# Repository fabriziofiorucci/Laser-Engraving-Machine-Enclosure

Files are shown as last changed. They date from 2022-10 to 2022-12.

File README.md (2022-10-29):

# Laser Engraving Machine Enclosure

This is an enclosure project to safely run a 450mm x 450mm laser engraving open frame machine.
The project was originally built around Sculpfun S9 but is suitable for all laser engraving machines with a footprint up to 450mm x 450mm.

Features:

- Full enclosure to protect from laser beam
- Air assist support
- Camera support to keep track of ongoing engraving/cutting jobs
- Internal lighting
- Fumes exhaust system
- Controlled by Wemos Lolin D1 mini
  - Pushbuttons and OLED display
  - Fumes exhaust system start/stop
  - Air assist start/stop
  - Laser engraver start/stop
- MQTT support (work in progress)

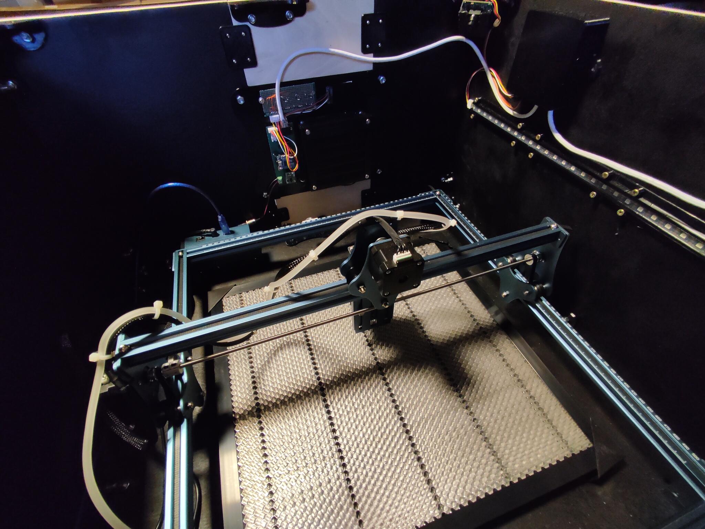
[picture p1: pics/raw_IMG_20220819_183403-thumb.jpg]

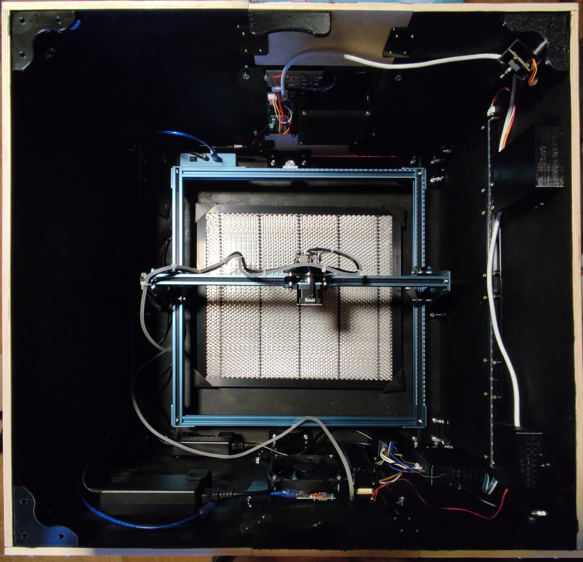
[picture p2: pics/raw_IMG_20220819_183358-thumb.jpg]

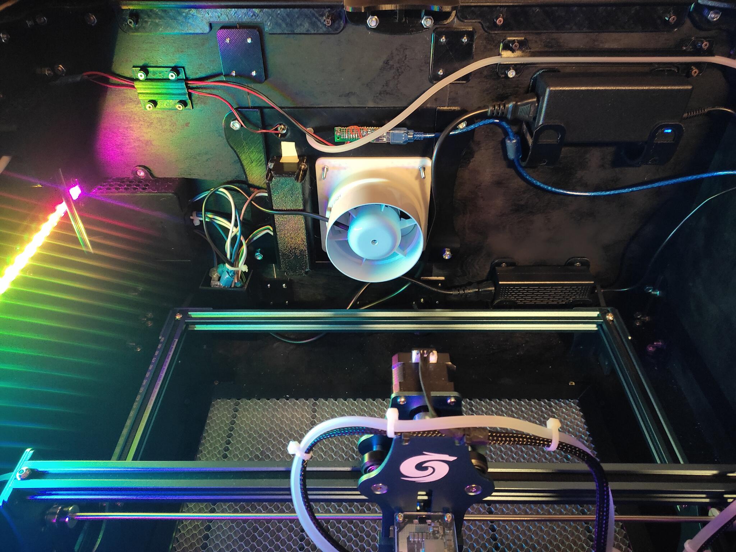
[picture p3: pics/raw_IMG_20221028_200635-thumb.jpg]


## Main structure

The main structure is built with 10mm-thick medium-density fiberboard (MDF) panels, spray-painted black.

## 3D Printed parts

The complete Fusion 360 project can be found in the [CAD folder](/CAD) and it can be opened in Autodesk Fusion 360.

3D parts should be printed using:

- Black PLA or PETG
- 20% infill
- 0.1mm layer width
- 4 walls
- No supports required for most parts

## Microcontroller

The [sketch](/sketch) can be flashed to Wemos Lolin D1 mini using Arduino 1.8.7 or later

NOTE: don't forget to use the provided User_Setup.h instead of the stock file that comes with the TFT_eSPI library

Required external libraries are:

- PCF8574 library by Renzo Mischianti - https://www.mischianti.org/2019/01/02/pcf8574_1-i2c-digital-i-o-expander-fast-easy-usage/
- APA102 by Pololu
- TFT_eSPI by Bodmer
- PubSubClient by Nick O'Leary
- NTPClient by Fabrice Weinberg

Display bitmaps have been generated using [LCD Image Converter](https://sourceforge.net/projects/lcd-image-converter/)

## Bill of Materials

### Main structure:

- 2x MDF boards 700mm x 700mm x 10mm
- 2x MDF boards 700mm x 400mm x 10mm
- 2x MDF boards 400mm x 300mm x 10mm
- 2x MDF boards 400mm x 200mm x 10mm
- 4x MDF boards 200mm x 100mm x 10mm
- Black spray paint ([RAL 9005](https://www.ralcolorchart.com/ral-classic/ral-9005-jet-black), approx 800ml needed)

### 3D-printed parts:

- 2kg black PLA or PETG filament

### Air Assist:

- 1x Hailea Air Compressor ACO-318 or equivalent (60L/min, 230V)
- Flexible air-line aquarium tubing, 4mm inner diameter, 6mm outer diameter

### Fumes exhaust system:

- 2x 120mm 12v PC fan
- 1x Airope BA 100mm Axial inline 100mm diameter fumes extractor fan or equivalent
- 1x Flexible Fume Hood Duct 102mm diameter

### Electronics:

Full schematics are [available here](/schematics). All boards built on single-sided protoboard.

#### Main board

- 1x Wemos Lolin D1 mini
- 1x MP1584EN (DC-DC 3A step-down)
- 1x PCF8574 (I2C I/O expansion module)
- 1x P82B715PN (I2C bus extender)
- 1x 2-pin PCB terminal block
- 1x RJ45 8p8c 90 degree angle PCB connector
- 1x 5-pin JST XH2.54 PCB terminal connector
- 1x 4-pin JST XH2.54 PCB terminal connector
- 1x 2-pin JST XH2.54 PCB terminal connector
- 1x 2n2222a transistor
- 3x 1kOhm 1/4w resistor
- 2x 430Ohm 1/4w resistor
- 2x 4.7kOhm 1/4w resistor
- 1x 1n4148 diode
- 1x 8pin DIP socket
- 1x 16pin DIP socket

#### Control and display board

- 1x IPS LCD 1.3" 240×240 RGB Display ST7789 (ie. https://protosupplies.com/product/ips-lcd-1-3-240x240-rgb-display-st7789/)
- 3x 4-pin tactile pushbutton momentary switch with switch cap (ie. https://www.amazon.com/TWTADE-Momentary-Tactile-Button-12x12x12mm/dp/B07CG7VTGD)
- 1x 5-pin JST XH2.54 PCB terminal connector
- 3x 0.1uF capacitor
- 3x 100kOhm 1/4w resistor
- 3x 10kOhm 1/4w resistor

#### Port expander board

- 1x MP1584EN (DC-DC 3A step-down)
- 1x PCF8574 (I2C I/O expansion module)
- 1x P82B715PN (I2C bus extender)
- 2x RJ45 8p8c 90 degree angle PCB connector
- 1x 3-pin JST XH2.54 PCB terminal connector
- 1x 4-pin JST XH2.54 PCB terminal connector
- 2x 2n2222a transistor
- 6x 1kOhm 1/4w resistor
- 2x 430Ohm 1/4w resistor
- 2x 4.7kOhm 1/4w resistor
- 1x 1n4148 diode
- 1x 8pin DIP socket
- 1x 16pin DIP socket

#### Port splitter board

- 1x RJ45 8p8c 90 degree angle PCB connector
- 1x 2-pin JST XH2.54 PCB terminal connector

#### Relay board

- 1x 5v Relay board 4 channels

#### Other / miscellaneous

- 1x APA102 RGB LED weatherproof strip (38 LEDs needed)
- 1x 1/3" 480TVL CCD, 12v color camera board with analog output or equivalent (ie. https://www.aliexpress.com/item/1005004590992499.html)
- 1x RCA female panel mount connector
- 1x micro USB to DIP adapter (ie. https://www.aliexpress.com/item/32970950859.html)
- 1x USB Type A female PCB connector
- 0.1" Strip male headers
- CAT6 cable
- RJ45 8p8c plugs for CAT6 cable

### Hardware:

- M3, M4 and M6 torx screws
- M3, M4 and M6 nuts
- Zip ties

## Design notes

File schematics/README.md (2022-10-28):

# Electronic schematics

All schematics created with [EasyEDA](https://easyeda.com).
Boards can be built using single-sided protoboard

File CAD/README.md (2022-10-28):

# Autodesk Fusion 360 project files

These files can be opened in Fusion 360 to generate stl output for 3D printing.

3D parts should be printed using:

- Black PLA or PETG
- 20% infill
- 4 walls
- No supports required for most parts

[STL files](/CAD/stl) are provided as well.

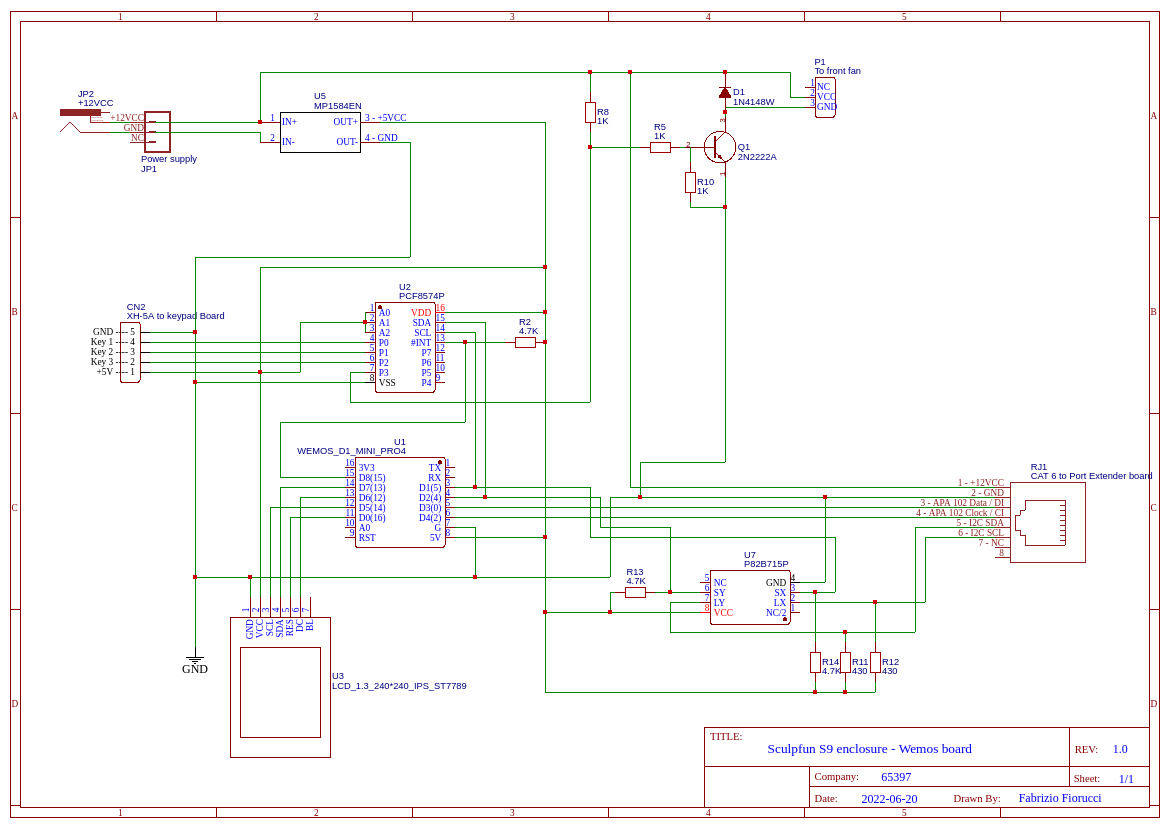
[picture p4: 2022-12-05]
schematics/Wemos board.png

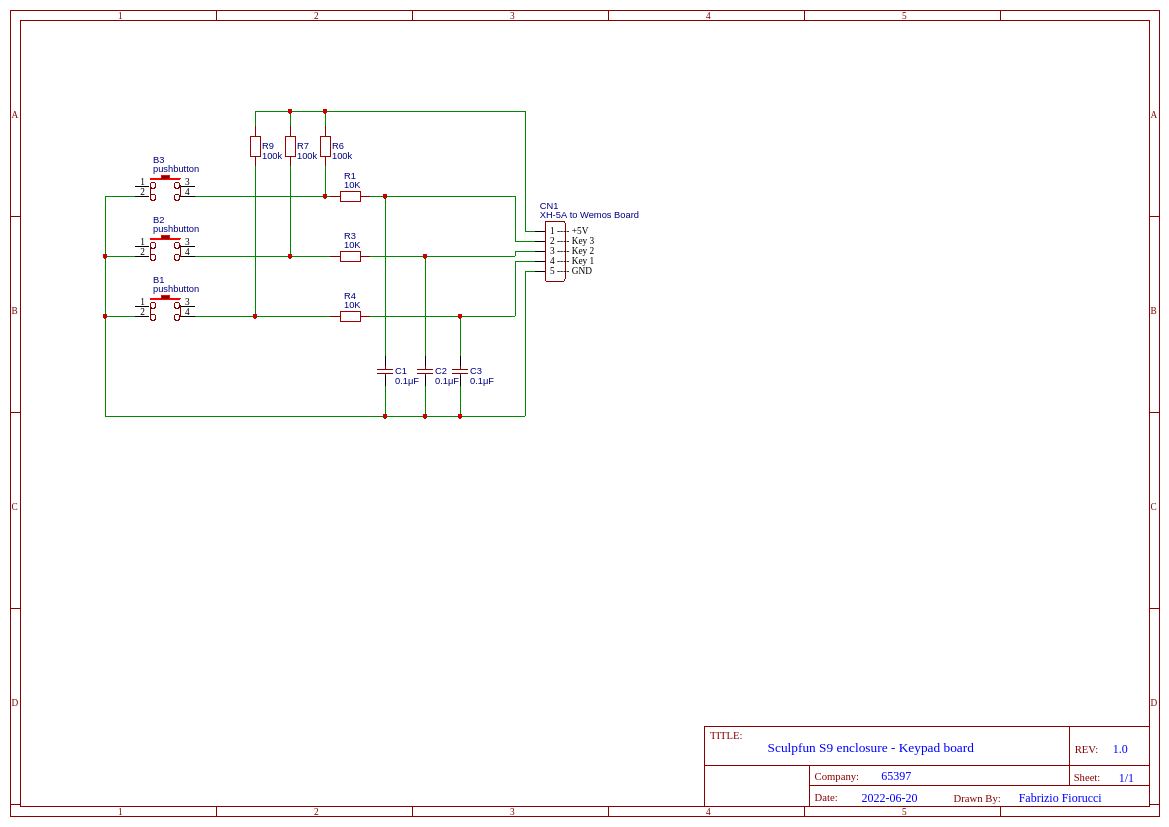
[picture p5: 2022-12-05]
schematics/Keypad board.png

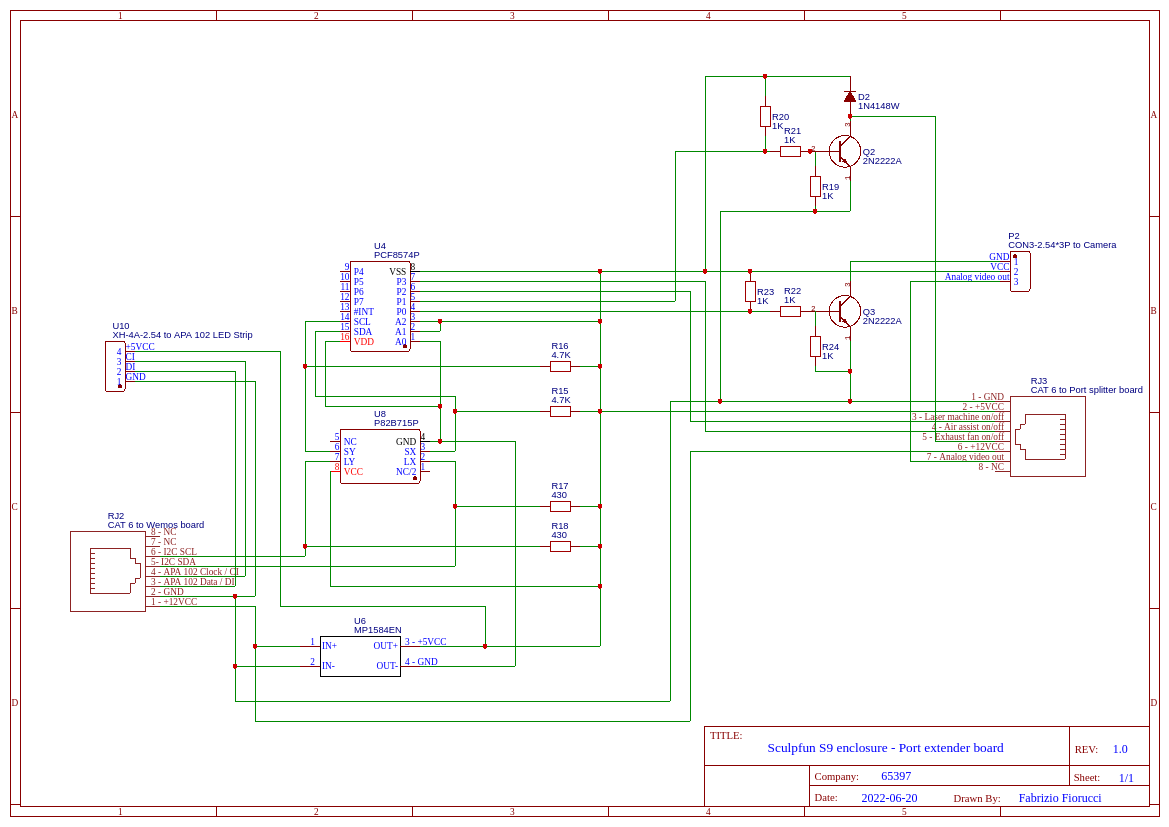
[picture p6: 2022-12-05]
schematics/Port extender board.png

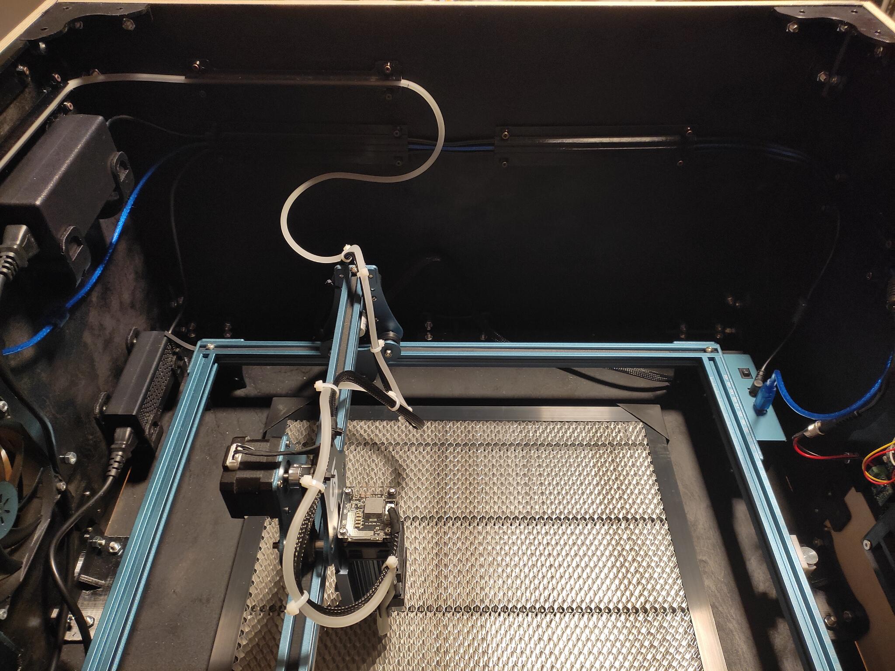
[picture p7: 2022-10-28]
pics/raw_IMG_20220917_213138-thumb.jpg

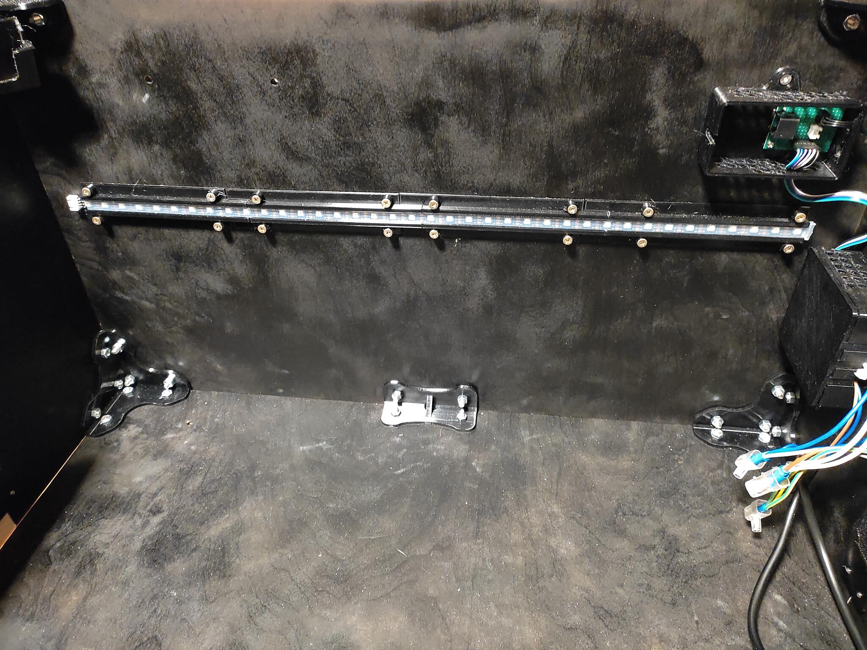
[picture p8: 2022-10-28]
pics/raw_IMG_20220808_000309-thumb.jpg

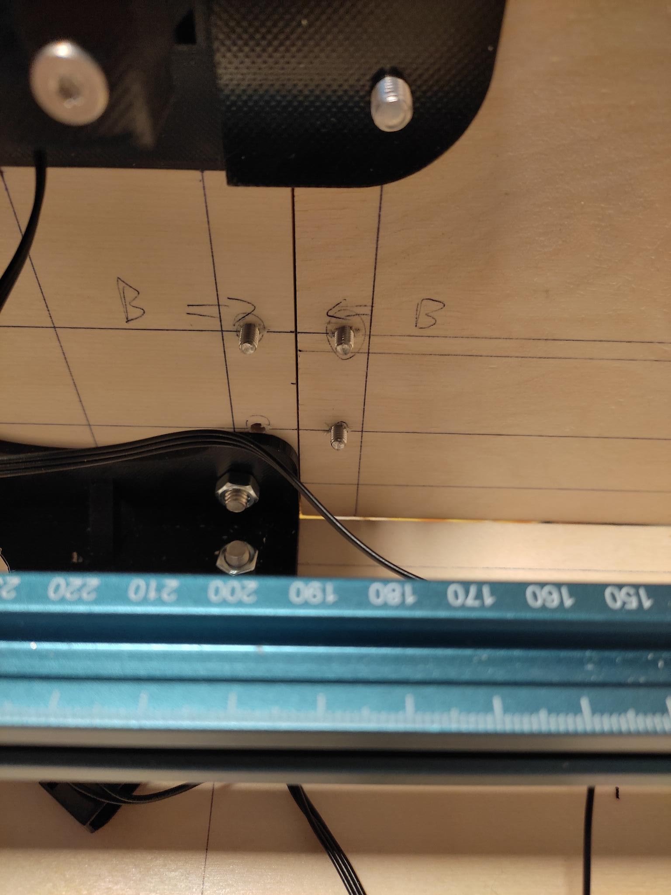
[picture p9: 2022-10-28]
pics/raw_IMG_20220528_145532-thumb.jpg

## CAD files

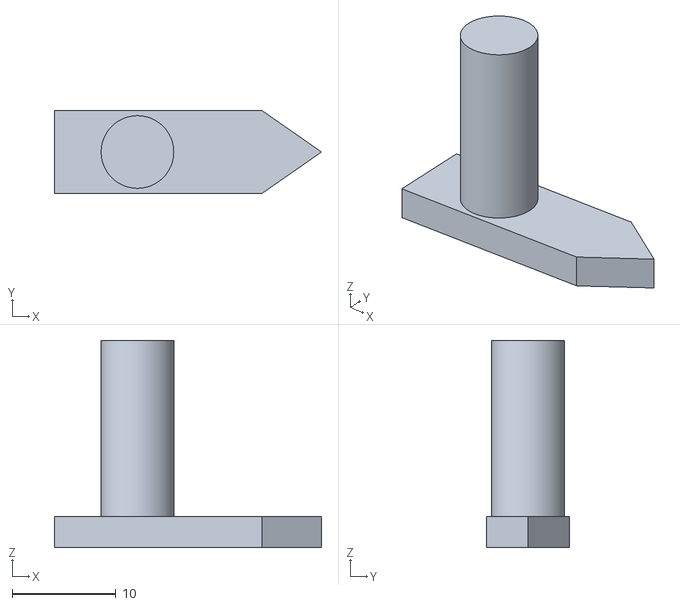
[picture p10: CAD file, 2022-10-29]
CAD/stl/Honeycomb bed pin.stl
25.7 x 8.00 x 20.0

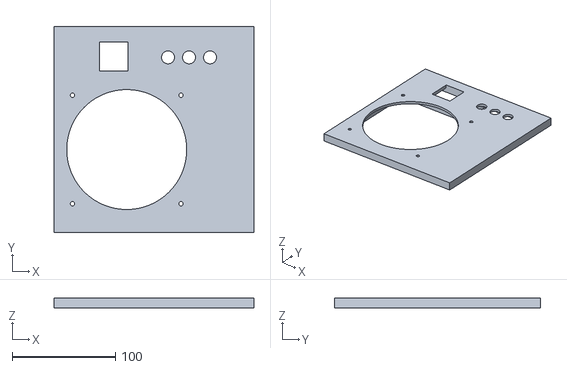
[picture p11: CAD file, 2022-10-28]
CAD/stl/Front panel.stl
193.5 x 199.5 x 10.0

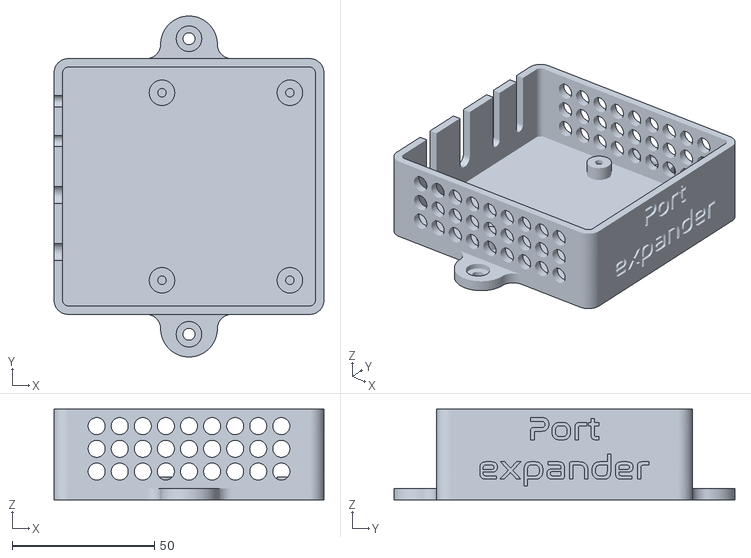
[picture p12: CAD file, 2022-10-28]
CAD/stl/Port expander base.stl
95.0 x 120.0 x 32.0

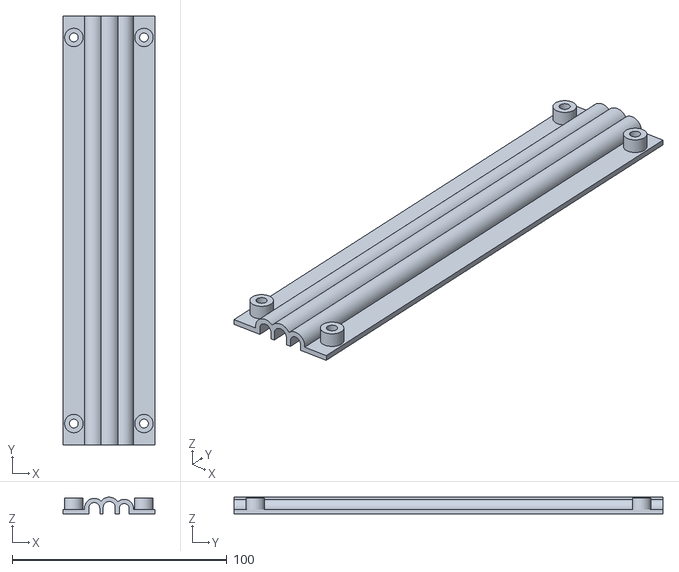
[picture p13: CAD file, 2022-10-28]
CAD/stl/Power and USB cable guide.stl
42.8 x 200.0 x 7.80

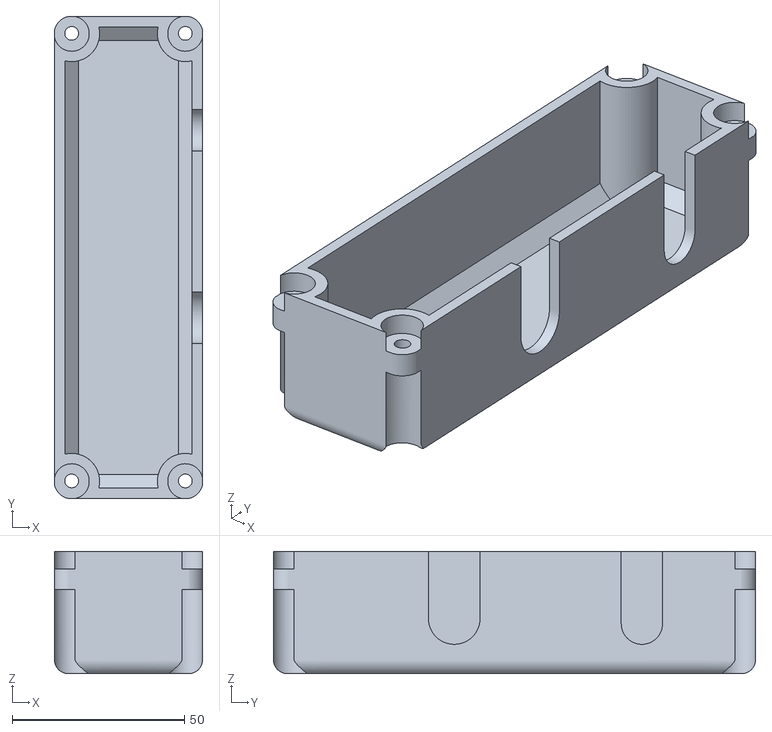
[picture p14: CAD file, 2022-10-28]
CAD/stl/Back panel 220v lid.stl
43.0 x 140.0 x 35.5

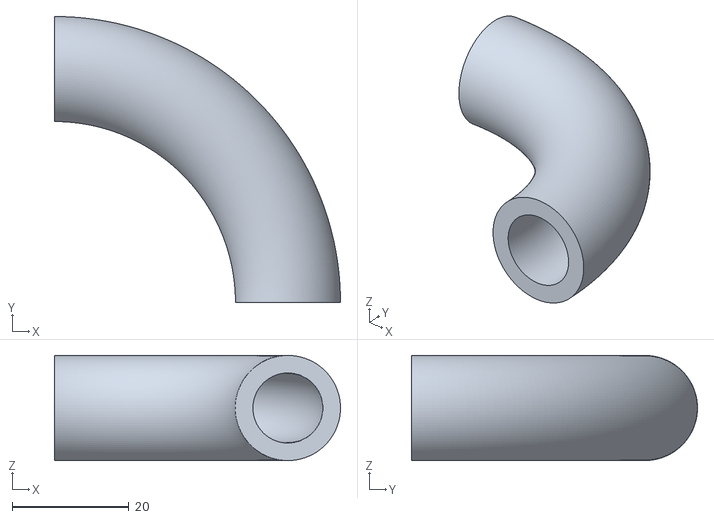
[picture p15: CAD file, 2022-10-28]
CAD/stl/Air compressor guide.stl
49.0 x 49.0 x 18.0

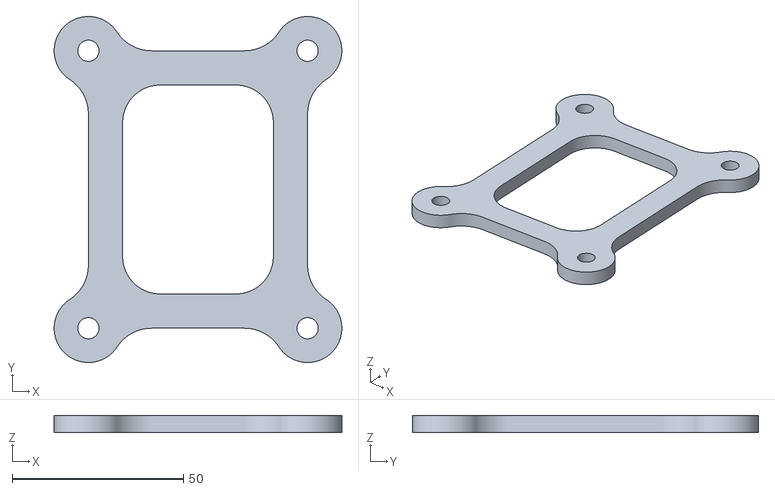
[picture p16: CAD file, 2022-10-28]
CAD/stl/Air compressor bracket.stl
84.0 x 101.0 x 5.00

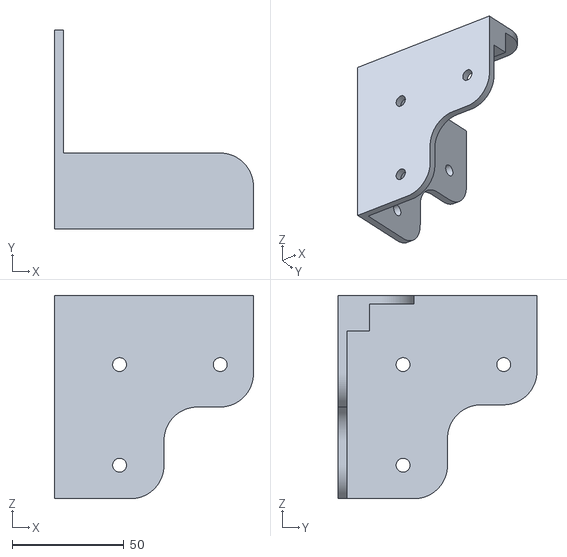
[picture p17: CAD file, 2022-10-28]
CAD/stl/Top cover corner lock 1.stl
89.0 x 89.0 x 91.0

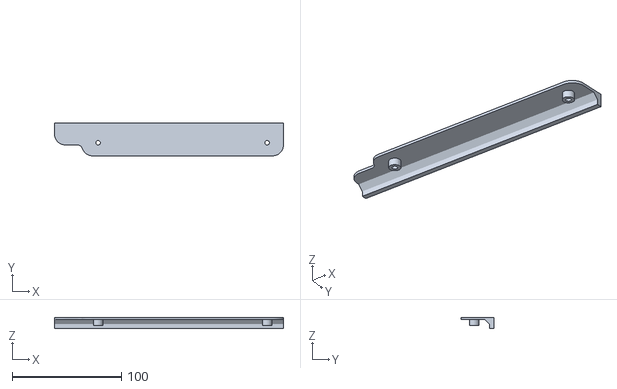
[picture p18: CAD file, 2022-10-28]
CAD/stl/Darkening corner 2.stl
210.0 x 30.0 x 10.0

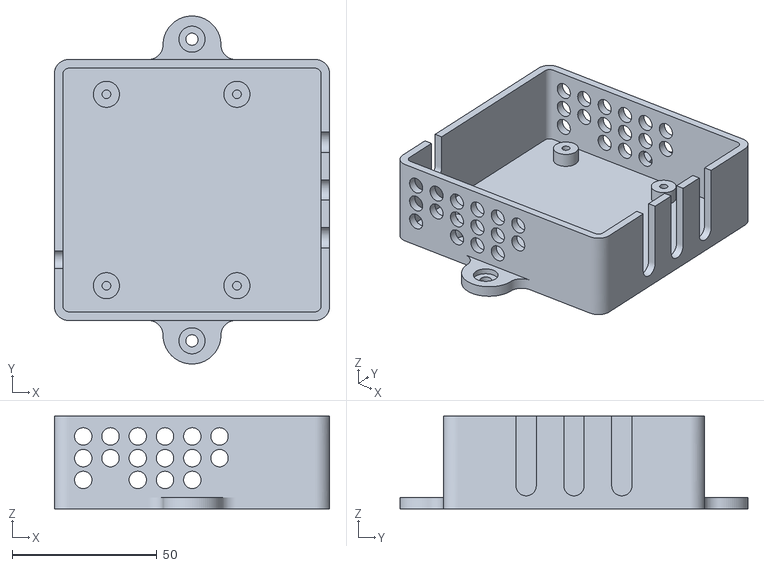
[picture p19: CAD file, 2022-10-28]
CAD/stl/Relay box base.stl
95.0 x 120.0 x 32.0

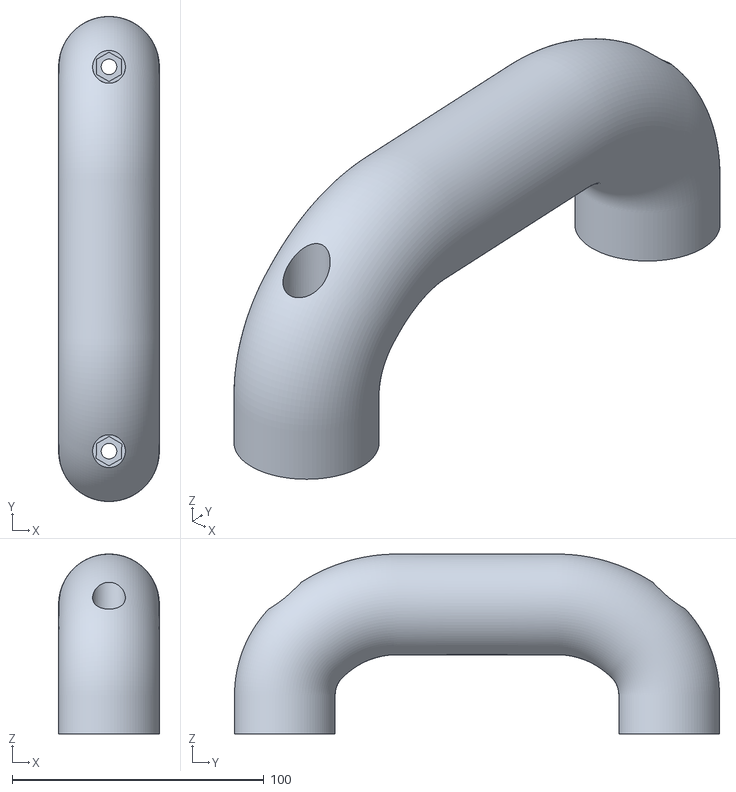
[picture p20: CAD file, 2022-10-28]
CAD/stl/Top handle v8.stl
40.0 x 192.5 x 71.4

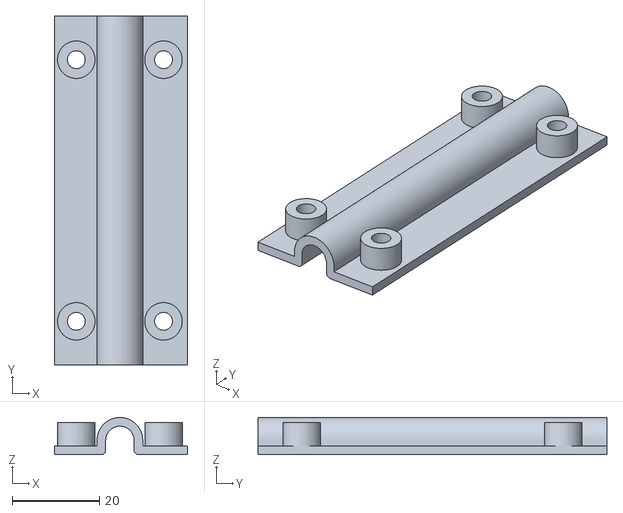
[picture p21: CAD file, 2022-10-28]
CAD/stl/Cat 6 cable guide.stl
30.5 x 80.0 x 8.50

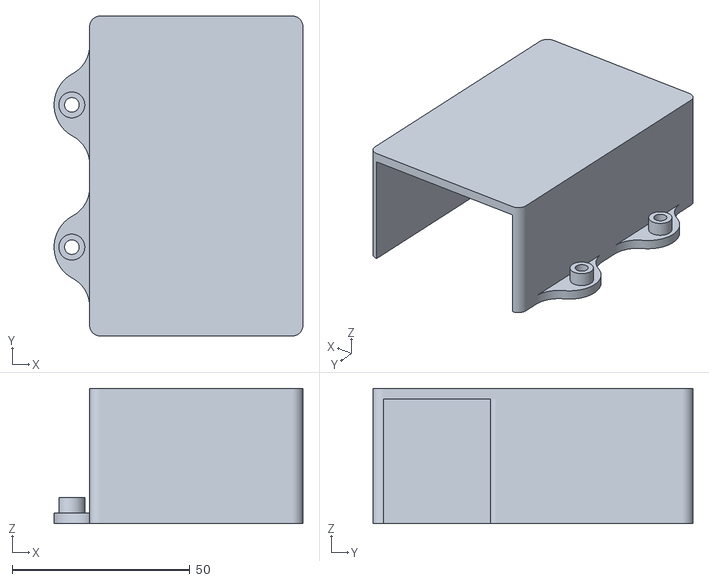
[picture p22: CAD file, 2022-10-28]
CAD/stl/230V protection shell v12.stl
70.0 x 90.0 x 38.0

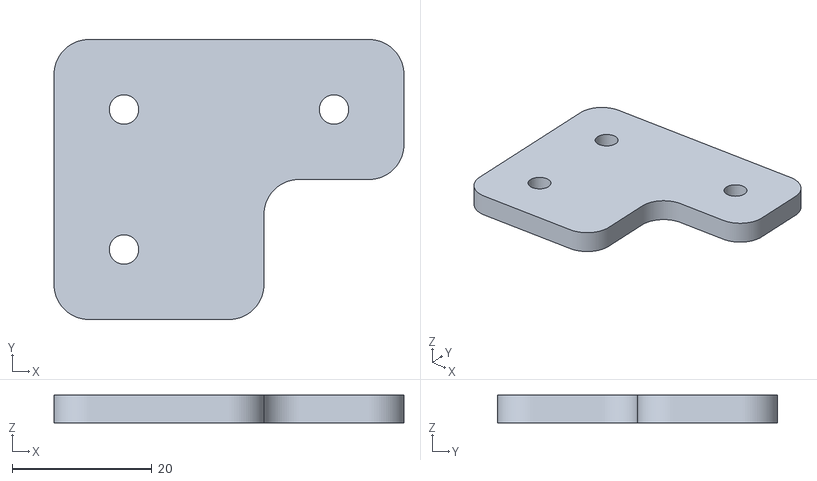
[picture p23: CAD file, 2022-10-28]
CAD/stl/Panel holder mini 3 holes v2.stl
50.0 x 40.0 x 4.00

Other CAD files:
CAD/stl/Camera output and fan cables.stl
CAD/stl/USB port lid.stl
CAD/stl/Exhaust pipe bracket v7.stl
CAD/stl/PSU 8A holder v17Left.stl
CAD/Exhaust pipe external bracket v9.f3d
CAD/Honeycomb bed pin v2.f3d
CAD/Laser air tube clip v11.f3d
CAD/stl/APA102 Led guide end v4.stl
CAD/stl/APA102 Led guide mid v7.stl
CAD/stl/APA102 Led guide start v12.stl
CAD/stl/Air pipe guide 200mm.stl
CAD/stl/Back Panel.stl
CAD/stl/Camera bracket v25.stl
CAD/stl/Corner bracket v22.stl
CAD/stl/Darkening corner 1.stl
CAD/stl/Darkening corner style 2.1.stl
CAD/stl/Darkening corner style 2.2.stl
CAD/stl/Display holder.stl
CAD/stl/Exhaust pipe bracket no holes v1.stl
CAD/stl/Exhaust pipe external bracket.stl
CAD/stl/Fan deflector.stl
CAD/stl/Laser air tube clip v11.stl
CAD/stl/Mid bracket.stl
CAD/stl/PSU 5A holder v6 Left.stl
CAD/stl/PSU 5A holder v6 Right.stl
CAD/stl/PSU 8A holder v17 Right.stl
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

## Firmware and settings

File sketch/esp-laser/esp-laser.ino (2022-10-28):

/*
 * ESP Laser - Laser CNC enclosure controller - 2022 Fabrizio Fiorucci
 */

// TFT_eSPI library used for 240x240 OLED display
// Based on this tutorial
// https://www.instructables.com/id/Converting-Images-to-Flash-Memory-Iconsimages-for-/
// https://github.com/STEMpedia/eviveProjects/blob/master/imageToFlashMemoryIconsForTFT/
// Don't forget to change User_Setup.h inside TFT_eSPI library !

// PCF8574 library by Renzo Mischianti - https://www.mischianti.org/2019/01/02/pcf8574_1-i2c-digital-i-o-expander-fast-easy-usage/
// APA102 by Pololu
// TFT_eSPI by Bodmer - Bitmaps generated with LCD Image Converter - https://sourceforge.net/projects/lcd-image-converter/
// PubSubClient by Nick O'Leary
// NTPClient by Fabrice Weinberg

#include <EEPROM.h>
#include <ESP8266WiFi.h>
#include <PubSubClient.h>
#include <NTPClient.h>
#include <WiFiUdp.h>
#include <ArduinoOTA.h>
#include <TFT_eSPI.h>
#include "boot.h"
#include "aircompressor.h"
#include "fan.h"
#include "laserbeam.h"
#include "lasercnc.h"
#include "PCF8574.h"
#include <APA102.h>

// Custom parameters - TO BE EDITED
const char * ssid = "MY_ESSID";
const char * password = "MY_ESSID_PASSWORD";

const char * mqttServer = "MQTT_SERVER_IP_ADDRESS";
const char * mqttClientId = "esp-laser";
const char * mqttClientPassword = "MQTT_PASSWORD";
const char * otaName = "esp-laser";
const char * otaPassword = "OTA_PASSWORD";
const char * ntpServer = "NTP_SERVER_IP_ADDRESS";

const char * controlTopic = "esp-laser/control";
const char * debugTopic = "esp-laser/debug";

// WiFi
WiFiClient wifiClient;
PubSubClient mqttClient(wifiClient);
WiFiUDP ntpUDP;
NTPClient timeClient(ntpUDP, ntpServer, 3600, 60000);

// APA102
const uint8_t APA102_DATA = D3;
const uint8_t APA102_CLK = D4;

// Create an object for writing to the LED strip.
APA102<APA102_DATA, APA102_CLK> ledStrip;

// Set the number of LEDs to control.
const uint16_t ledCount = 38;
// Create a buffer for holding the colors (3 bytes per color).
rgb_color colors[ledCount];

// Set the brightness to use (the maximum is 31).
const uint8_t brightness = 8;

// TFT display
TFT_eSPI tft = TFT_eSPI();
TFT_eSprite sprite_boot = TFT_eSprite(&tft);
TFT_eSprite sprite_aircompressor = TFT_eSprite(&tft);
TFT_eSprite sprite_fan = TFT_eSprite(&tft);
TFT_eSprite sprite_laserbeam = TFT_eSprite(&tft);

#define TFT_MOSI  13  // D7
#define TFT_SCK 14    // D5
#define TFT_CS -1     // Not used
#define TFT_DC  12    // D6
#define TFT_RESET 16  // D0

// PCF8574 I2C port expanders
PCF8574 pcf8574_mainboard(0x27);
PCF8574 pcf8574_portextender(0x26);

long lastMsg = 0;
long pollInterval = 1000;

// Buttons are active low
int button1 = 1;
int button2 = 1;
int button3 = 1;

boolean isFanOn=false;
boolean isLaserOn=false;
boolean isWebcamOn=false;
boolean isAirAssistOn=false;

void setup_wifi() {
  delay(10);

  pinMode(LED_BUILTIN, OUTPUT);

  Serial.println();
  Serial.print("Connecting to ");
  Serial.println(ssid);

  WiFi.mode(WIFI_STA);
  WiFi.begin(ssid, password);

  for (int i = 0; i < 500 && WiFi.status() != WL_CONNECTED; i++) {
    digitalWrite(LED_BUILTIN, LOW);
    delay(25);
    digitalWrite(LED_BUILTIN, HIGH);
    delay(25);
    Serial.print(".");
  }

  if (WiFi.status() != WL_CONNECTED) {
    Serial.print("Restarting ESP due to loss of Wi-Fi");
    ESP.restart();
  }

  randomSeed(micros());

  Serial.println("");
  Serial.print("WiFi connected to ");
  Serial.println(ssid);
  Serial.print("IP address: ");
  Serial.println(WiFi.localIP());
}

void reconnectMqtt() {
  while (!mqttClient.connected()) {
    String clientId = mqttClientId;

    Serial.print("Attempting MQTT connection...");

    if (mqttClient.connect((char * ) String(ESP.getChipId()).c_str(), mqttClientId, mqttClientPassword)) {
      Serial.println("connected to MQTT");
      mqttClient.subscribe(controlTopic);
      mqttClient.setBufferSize(1024);
    } else {
      Serial.print("failed, rc=");
      Serial.print(mqttClient.state());
      Serial.println(" try again in 3 seconds");
      delay(3000);
    }
  }
}

void IRAM_ATTR callback(char * topic, byte * payload, unsigned int length) {
  if (strcmp(topic,controlTopic)==0) {
    char cmd = (char)payload[0];
    if (cmd=='R') {
      ESP.restart();
    }
  }
}

/* Converts a color from HSV to RGB.
 * h is hue, as a number between 0 and 360.
 * s is the saturation, as a number between 0 and 255.
 * v is the value, as a number between 0 and 255. */
rgb_color hsvToRgb(uint16_t h, uint8_t s, uint8_t v)
{
    uint8_t f = (h % 60) * 255 / 60;
    uint8_t p = (255 - s) * (uint16_t)v / 255;
    uint8_t q = (255 - f * (uint16_t)s / 255) * (uint16_t)v / 255;
    uint8_t t = (255 - (255 - f) * (uint16_t)s / 255) * (uint16_t)v / 255;
    uint8_t r = 0, g = 0, b = 0;
    switch((h / 60) % 6){
        case 0: r = v; g = t; b = p; break;
        case 1: r = q; g = v; b = p; break;
        case 2: r = p; g = v; b = t; break;
        case 3: r = p; g = q; b = v; break;
        case 4: r = t; g = p; b = v; break;
        case 5: r = v; g = p; b = q; break;
    }
    return rgb_color(r, g, b);
}


void setup(void) {
  // EEPROM init
  EEPROM.begin(512);

  Serial.begin(115200, SERIAL_8N1);
  Serial.println("-----------------------------------------");
  Serial.printf("Chip ID     : %08X\n", ESP.getChipId());
  Serial.printf("Core version: %s\n", ESP.getCoreVersion().c_str());
  Serial.printf("SDK version : %s\n", ESP.getSdkVersion());
  Serial.printf("CPU speed   : %dMhz\n", ESP.getCpuFreqMHz());
  Serial.printf("Free Heap   : %d\n", ESP.getFreeHeap());
  Serial.printf("Reset reason: %s\n", ESP.getResetReason().c_str());
  Serial.printf("EEPROM size : %d\n", EEPROM.length());
  Serial.println("-----------------------------------------");

  Serial.println("Laser CNC controller init");

  // Display initialization
  tft.begin();     // initialize a ST7789 chip
  tft.setSwapBytes(true); // Swap the byte order for pushImage() - corrects endianness
  tft.setRotation(3);
  tft.fillScreen(TFT_WHITE);

  tft.pushImage(0,0,240,240,lasercncimage);
  delay(1000);
  tft.fillScreen(TFT_WHITE);

  sprite_boot.setColorDepth(4); // Optionally set depth to 8 to halve RAM use
  sprite_boot.createSprite(240,240);
  sprite_boot.setTextSize(1);

  sprite_boot.fillSprite(TFT_WHITE);
  sprite_boot.setTextColor(TFT_BLACK, TFT_WHITE);
  sprite_boot.drawString("Laser CNC startup", 0, 0, 2);
  sprite_boot.drawString("Connecting to Wi-Fi...", 0, 16, 2);
  sprite_boot.pushSprite(0, 0);

  // WiFi init
  setup_wifi();

  // NTP init
  timeClient.begin();

  sprite_boot.drawString("Connecting to MQTT Broker...",0,32,2);
  sprite_boot.pushSprite(0,0);

  // MQTT init
  mqttClient.setServer(mqttServer, 1883);
  mqttClient.setCallback(callback);
  mqttClient.setBufferSize(1024);
  reconnectMqtt();

  pcf8574_mainboard.pinMode(P0,OUTPUT, HIGH);
  pcf8574_mainboard.pinMode(P1,INPUT);
  pcf8574_mainboard.pinMode(P2,INPUT);
  pcf8574_mainboard.pinMode(P3,INPUT);

  pcf8574_portextender.pinMode(P0,OUTPUT);
  pcf8574_portextender.pinMode(P1,OUTPUT);
  pcf8574_portextender.pinMode(P2,OUTPUT);
  pcf8574_portextender.pinMode(P3,OUTPUT);

  delay(250);
  sprite_boot.drawString("Initializing mainboard I2C port expander...",0,48,2);
  sprite_boot.pushSprite(0,0);

  if (!pcf8574_mainboard.begin()) {
    Serial.println("PCF8574 @ 0x27 - mainboard error");

    sprite_boot.drawString("Mainboard I2C port expander FAILED",0,64,2);
    sprite_boot.pushSprite(0,0);

    delay(5000);
  } else {
    Serial.println("PCF8572 @ 0x27 - mainboard initialized");
  }

  delay(250);
  sprite_boot.drawString("Initializing daughterboard I2C port expander...",0,64,2);
  sprite_boot.pushSprite(0,0);

  if (!pcf8574_portextender.begin()) {
    Serial.println("PCF8574 @ 0x26 - port extender error");
    sprite_boot.drawString("Daughterboard I2C port expander FAILED",0,80,2);
    sprite_boot.pushSprite(0,0);

    delay(5000);
  } else {
    Serial.println("PCF8572 @ 0x26 - port extender initialized");
  }

  delay(250);
  sprite_boot.drawString("Setting default status to off...",0,80,2);
  sprite_boot.pushSprite(0,0);

  // Front fan off
  pcf8574_mainboard.digitalWrite(0,LOW);

  // Rear fan off
  pcf8574_portextender.digitalWrite(1,LOW);

  // Webcam off
  pcf8574_portextender.digitalWrite(0,LOW);

  // Laser CNC off
  pcf8574_portextender.digitalWrite(2,HIGH);

  // Air Assist off
  pcf8574_portextender.digitalWrite(3,HIGH);

  delay(250);
  sprite_boot.drawString("Initializing OTA...",0,96,2);
  sprite_boot.pushSprite(0,0);

  // OTA init
  ArduinoOTA.setPort(8266);
  ArduinoOTA.setHostname(otaName);
  ArduinoOTA.setPassword(otaPassword);

  ArduinoOTA.onStart([]() {
    Serial.println("OTA Start");
  });
  ArduinoOTA.onEnd([]() {
    Serial.println("OTA End");
  });
  ArduinoOTA.onProgress([](unsigned int progress, unsigned int total) {
    Serial.printf("OTA in progress %s", String(progress / (total / 100)));
  });
  ArduinoOTA.onError([](ota_error_t error) {
    Serial.printf("Error[%u]: ", error);
    if (error == OTA_AUTH_ERROR) Serial.println("OTA Auth failed");
    else if (error == OTA_BEGIN_ERROR) Serial.println("OTA Begin failed");
    else if (error == OTA_CONNECT_ERROR) Serial.println("OTA Connect failed");
    else if (error == OTA_RECEIVE_ERROR) Serial.println("OTA Receive failed");
    else if (error == OTA_END_ERROR) Serial.println("OTA End failed");
  });
  ArduinoOTA.begin();

  delay(250);
  tft.fillScreen(TFT_WHITE);

/*
  sprite_aircompressor.setColorDepth(8);
  sprite_aircompressor.createSprite(110,110);
  sprite_aircompressor.pushImage(0, 0, 110, 110, (uint16_t *)aircompressorimage);

  sprite_fan.setColorDepth(4);
  sprite_fan.createSprite(110,110);
  sprite_fan.pushImage(0, 0, 110, 110, (uint16_t *)fanimage);

  sprite_laserbeam.setColorDepth(4);
  sprite_laserbeam.createSprite(110,110);
  sprite_laserbeam.pushImage(0, 0, 110, 110, (uint16_t *)laserbeamimage);*/
}

void loop() {
  ArduinoOTA.handle();
  timeClient.update();

  if (!mqttClient.connected()) {
    reconnectMqtt();
  }

  mqttClient.loop();

  PCF8574::DigitalInput di = pcf8574_mainboard.digitalReadAll();
  if (di.p1!=button1 || di.p2!=button2 || di.p3!=button3) {
    Serial.printf("Buttons: %d %d %d\n",di.p1,di.p2,di.p3);

    if(button1!=di.p1 && button1==0) {
      if(!isFanOn) {
       Serial.println("Fan on");

       // Front fan on
       pcf8574_mainboard.digitalWrite(0,HIGH);

       // Read fan on
       pcf8574_portextender.digitalWrite(1,HIGH);

       tft.pushImage(0,0,110,110,fanimage);
     } else {
       Serial.println("Fan off");

       // Front fan off
       pcf8574_mainboard.digitalWrite(0,LOW);

       // Rear fan off
       pcf8574_portextender.digitalWrite(1,LOW);

       tft.fillRect(0,0,110,110,TFT_WHITE);
      }
      isFanOn=!isFanOn;
    }

    /*
    if(button2!=di.p2 && button2==0) {
      if(!isWebcamOn) {
       Serial.println("Webcam on");

       // Webcam on
       pcf8574_portextender.digitalWrite(0,HIGH);
     } else {
       Serial.println("Webcam off");

       // Webcam off
       pcf8574_portextender.digitalWrite(0,LOW);
      }
      isWebcamOn=!isWebcamOn;
    }
    */

    if(button2!=di.p2 && button2==0) {
      if(!isAirAssistOn) {
       Serial.println("Air Assist on");

       // Air assist on
       pcf8574_portextender.digitalWrite(3,LOW);

       tft.pushImage(120,0,110,110,aircompressorimage);
       } else {
         Serial.println("Air Assist off");

         // Air assist off
         pcf8574_portextender.digitalWrite(3,HIGH);
         
         tft.fillRect(120,0,110,110,TFT_WHITE);
        }
        isAirAssistOn=!isAirAssistOn;
      }

    if(button3!=di.p3 && button3==0) {
          if(!isLaserOn) {
       Serial.println("Laser CNC on");

       // Laser CNC on
       pcf8574_portextender.digitalWrite(2,LOW);

       // Webcam on
       pcf8574_portextender.digitalWrite(0,HIGH);

       tft.pushImage(0,120,110,110,laserbeamimage);
     } else {
       Serial.println("Air/S9 off");

       // Laser CNC off
       pcf8574_portextender.digitalWrite(2,HIGH);

       // Webcam off
       pcf8574_portextender.digitalWrite(0,LOW);

       tft.fillRect(0,120,110,110,TFT_WHITE);
      }
      isLaserOn=!isLaserOn;
    }
    
    button1=di.p1;
    button2=di.p2;
    button3=di.p3;
  }

  uint8_t time = millis() >> 4;

  for(uint16_t i = 0; i < ledCount; i++)
  {
    uint8_t p = time - i * 8;
    colors[i] = hsvToRgb((uint32_t)p * 359 / 256, 255, 255);
  }

  ledStrip.write(colors, ledCount, brightness);

  delay(7);

  long now = millis();
  if (now - lastMsg > pollInterval) {
    lastMsg = now;
  }

}

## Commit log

2022-10-29 Added stl for honeycomb pin
    [Honeycomb bed pin.stl]
2022-12-05 Schematics bugfix
